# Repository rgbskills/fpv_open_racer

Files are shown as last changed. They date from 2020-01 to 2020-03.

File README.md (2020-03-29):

# Introduction
- Open source design for racing quad. You can download and modify the designs to your liking.
- **DXF** files are also available in `dxf/` - these are the files you send if you want to get them cut out of carbon (list of services are coming soon).
- **[Join our slack channel](https://join.slack.com/t/openfpvworkspace/shared_invite/enQtODgyMDY0MTgyNDAxLTNkYTExNzY0YzkxYjYwZTdiMzQ1MzkwNzc3OTJhODZiMTdiMTg1ZTQwYjM1NjA1ODZkYjUzNWY0YTA1NTUwZmE)**
- **[3D Preview](https://a360.co/2Fc0HBd)**
- **[Facebook page](https://www.facebook.com/openfpvcommunity)**

# Features
* **stretched X** - X=140 Y=180mm **wheelbase: 228mm** (more control on the roll axis)
* **Lots of space**, the idea is to have no zip ties and nothing attached to the top plate for easy servicing
* **Compatible with 5.1"** Props
* **Weight: 80g**
* **Arms can be easily swapped** without unscrewing the stack
* Both **20x20** and **30.5x30.5** Stack mounting options are supported
* **All screws are accessible** even after complete build
* **Easy stack access** - large 6mm holes on the bottom plate allows you to insert/remove screws that hold your stack without any hassle
* **28.5x45mm** hole pattern on the top plate to add Gopro mounts or any other 3d Printed add-ons
* **CNC Millable with 3mm bit**

# Recommendations
* Use a three level stack: ESC, FC, and the last level should contain your VTX and RX
* If you use a buzzer get a small 9*5.5mm one
* UFL or MMCX VTX antenna
* there are no zip tie slots for a reason
* Nothing should be mounted on the top plate unless its a stand alone component like an HD camera.

# Carbon parts
* **BASE plate - 2mm**
* **BOTTOM plate - 2mm**
* **TOP plate - 2mm**
* **ARM - 4mm**

# Bill of materials
* 4x 25mm Aluminium, standoffs [Banggood](https://www.banggood.com/Suleve-M3AS5-10Pcs-M3-25mm-Knurled-Standoff-Aluminum-Alloy-Anodized-Spacer-p-1118407.html?ID=223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)
* 8x 13-14mm M3 screws (arms) [Banggood](https://www.banggood.com/Suleve-M3CH10-50Pcs-M3-Carbon-Steel-Hex-Socket-Button-Round-Head-Cap-Screws-Bolts-4-20mm-Optional-Length-p-1232490.html?ID=513288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)
* 8x 6mm M3 screws (standoffs) [Banggood](https://www.banggood.com/Suleve-M3CH10-50Pcs-M3-Carbon-Steel-Hex-Socket-Button-Round-Head-Cap-Screws-Bolts-4-20mm-Optional-Length-p-1232490.html?ID=528721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)
* 8x M3 nylon insert nuts (arms) [Banggood](https://www.banggood.com/Suleve-CS1-50pcs-Carbon-Steel-Self-Locking-Hex-Nut-Nylon-Insert-Lock-Nut-M2M2_5M3M4M5M6M8M10M12-p-1499543.html?ID=514519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)
* 1x Buzzer [Banggood](https://www.banggood.com/5-PCS-Super-Loud-5V-Active-Alarm-Buzzer-Beeper-Tracker-95_5mm-for-Racing-Drone-p-1117207.html)
* 1x XT60 [Banggood](https://www.banggood.com/Amass-XT60-MaleFemale-Bullet-Connector-Plugs-For-RC-Lipo-Battery-p-929670.html)

# 3D printable parts
### (You can find all 3d printables under `accessories/3D/`)
* [Camera mount (micro)](https://www.thingiverse.com/thing:4080423)
- [XT60 mount](https://www.thingiverse.com/thing:4082915)

# Builds
Open Source - FPV racing frame

# Latest Render
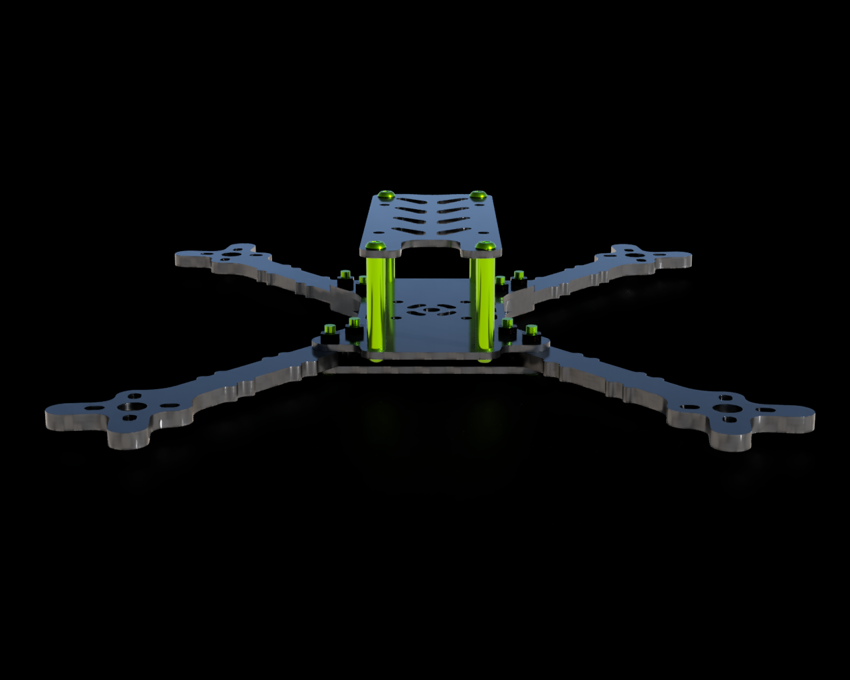
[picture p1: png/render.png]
Open Source - FPV racing frame


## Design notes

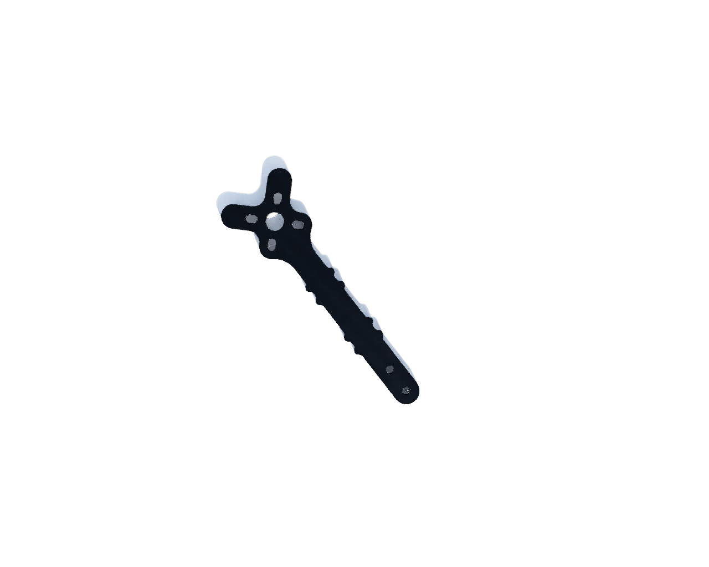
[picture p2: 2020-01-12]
png/ARM_4mm_4x.png

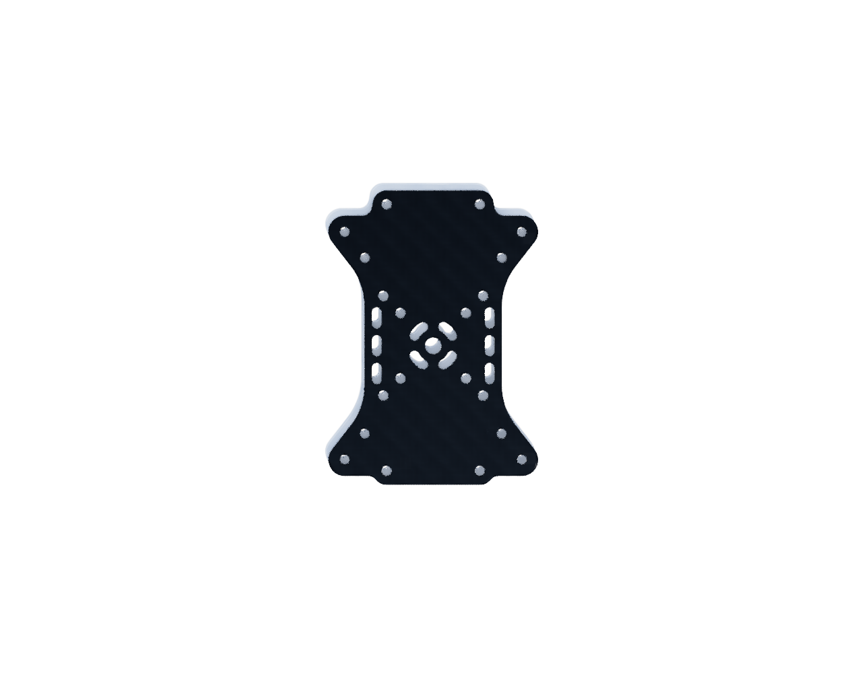
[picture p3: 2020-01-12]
png/BASE_2mm_1x.png

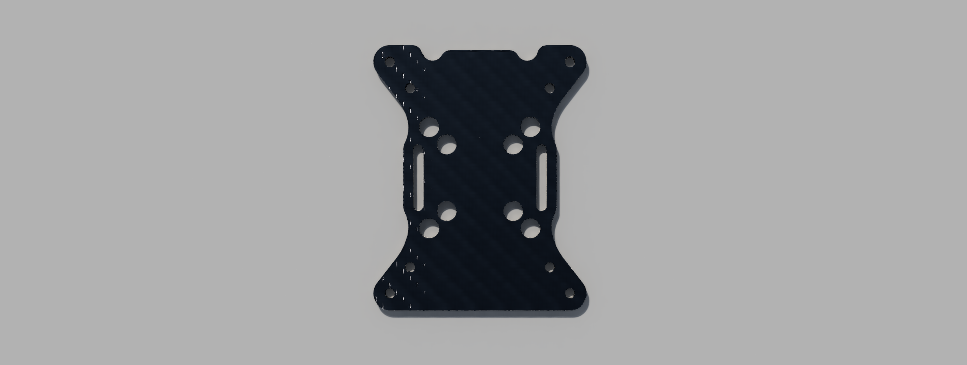
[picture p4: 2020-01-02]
png/BOTTOM_2mm_1x.png

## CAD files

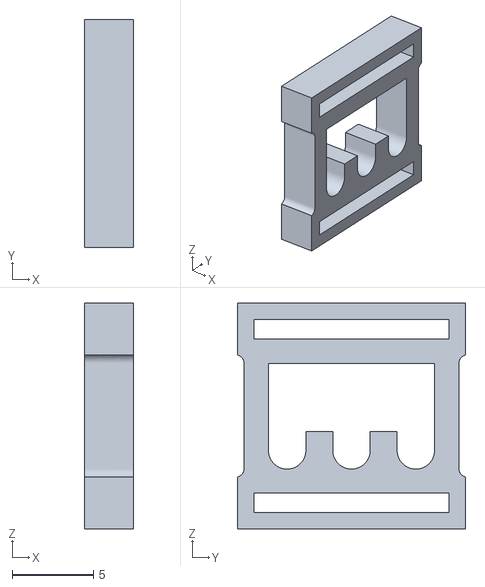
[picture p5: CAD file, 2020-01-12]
accessories/3D/cable_management_motor_ledTopBottom.stl
3.00 x 14.0 x 13.9

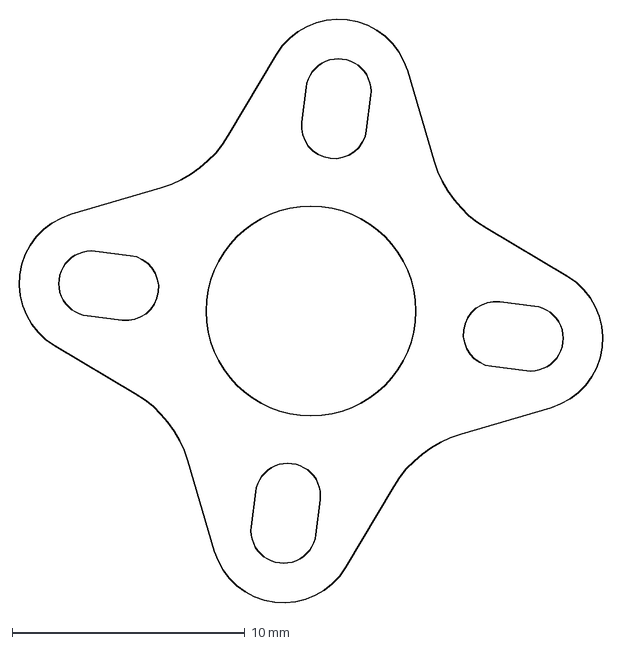
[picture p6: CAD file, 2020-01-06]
accessories/foamPads/motor_soft_mont.dxf
25.3 x 25.3 mm

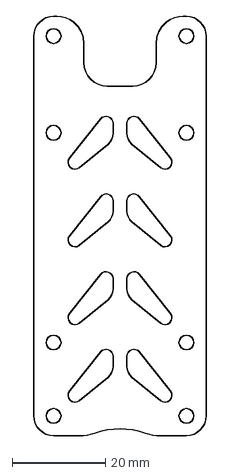
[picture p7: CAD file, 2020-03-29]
dxf/TOP_2mm_1x.dxf
37.0 x 90.0 mm

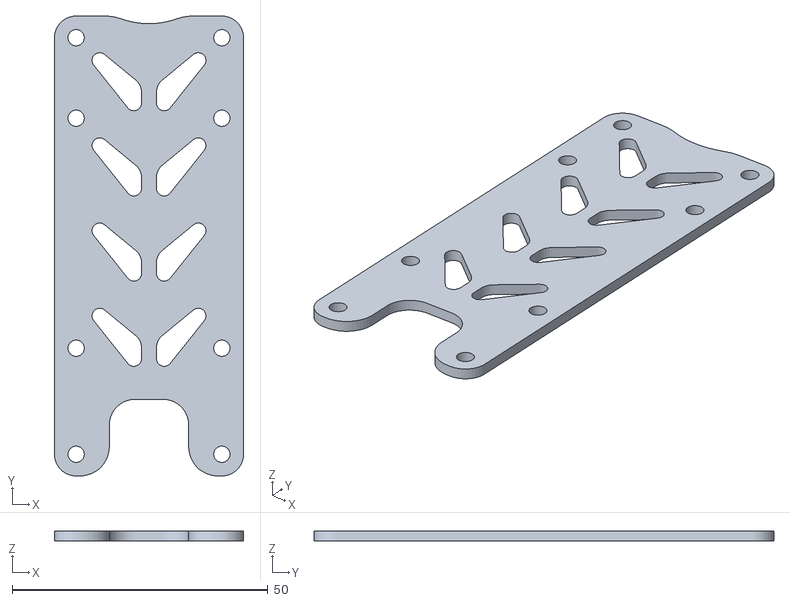
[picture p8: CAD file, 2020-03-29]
stl/top.stl
37.0 x 90.0 x 2.00

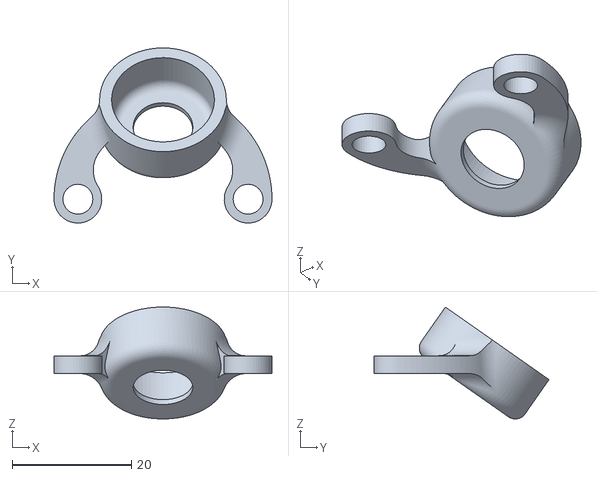
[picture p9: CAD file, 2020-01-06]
accessories/3D/mount_lolipop_UFL_MMCX.stl
36.5 x 29.3 x 18.7

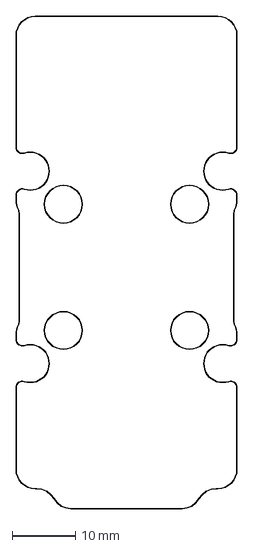
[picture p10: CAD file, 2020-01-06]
accessories/foamPads/bottom_plate_battery.dxf
35.0 x 78.0 mm

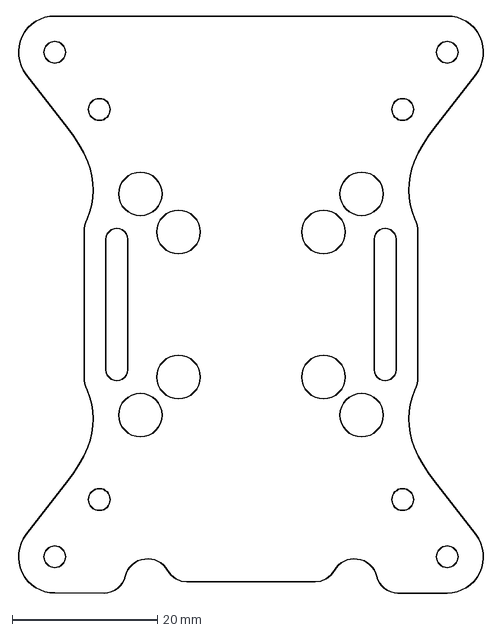
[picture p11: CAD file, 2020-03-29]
dxf/BOTTOM_2mm_1x.dxf
64.8 x 79.6 mm

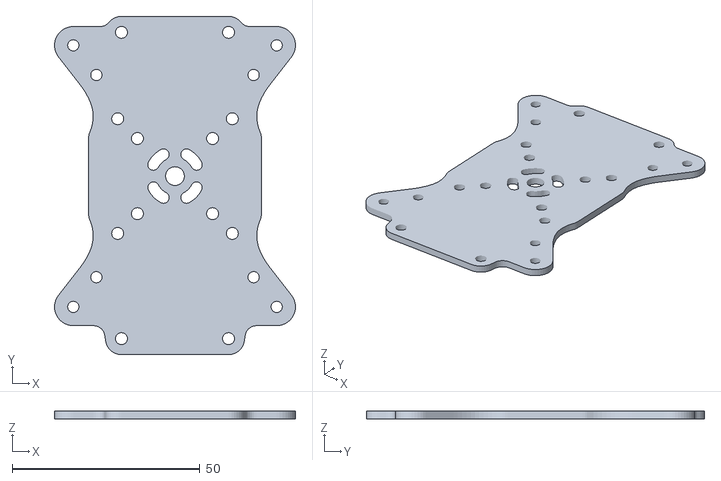
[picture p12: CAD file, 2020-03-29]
stl/base.stl
64.1 x 90.0 x 2.00

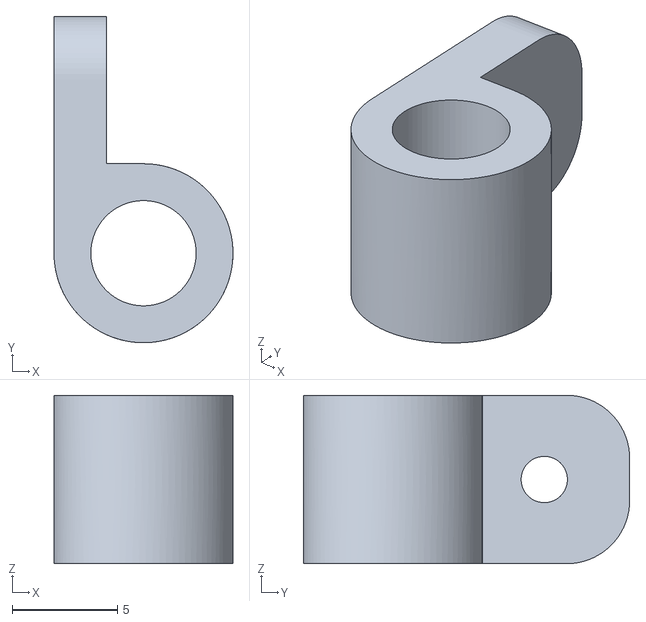
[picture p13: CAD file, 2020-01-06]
accessories/3D/mount_fpv_camera.stl
8.50 x 15.5 x 8.00

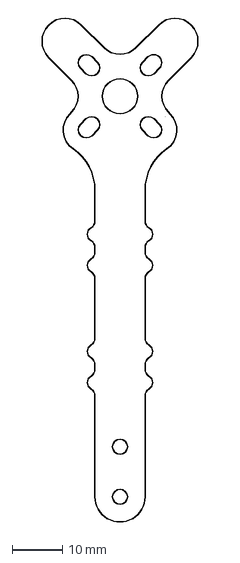
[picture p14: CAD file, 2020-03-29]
dxf/ARM_4mm_4x.dxf
32.0 x 101.2 mm

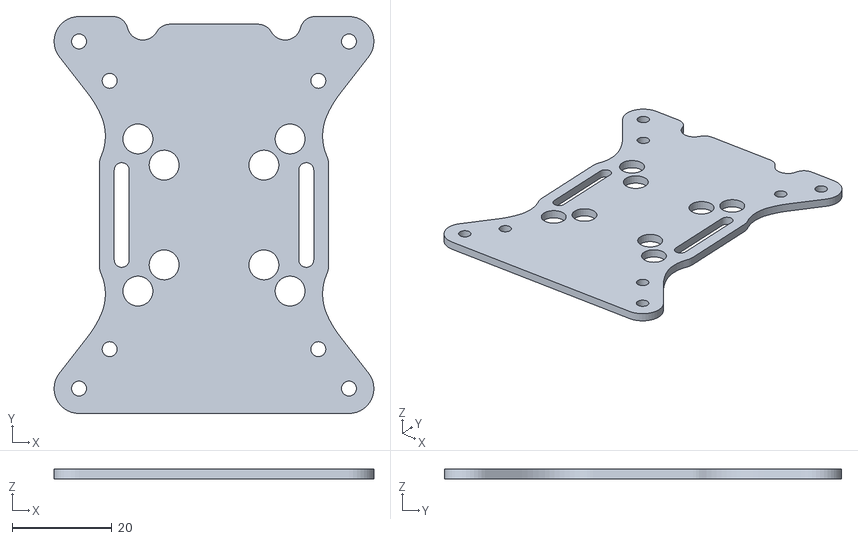
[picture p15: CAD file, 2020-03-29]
stl/bottom.stl
64.1 x 79.6 x 2.00

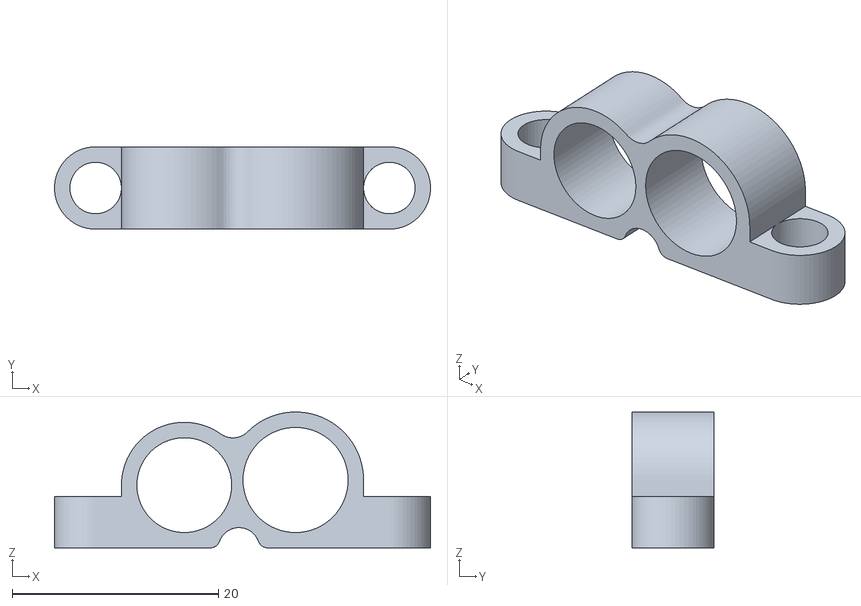
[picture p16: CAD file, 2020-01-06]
accessories/3D/mount_buzzer_capacitor.stl
36.5 x 8.00 x 13.2

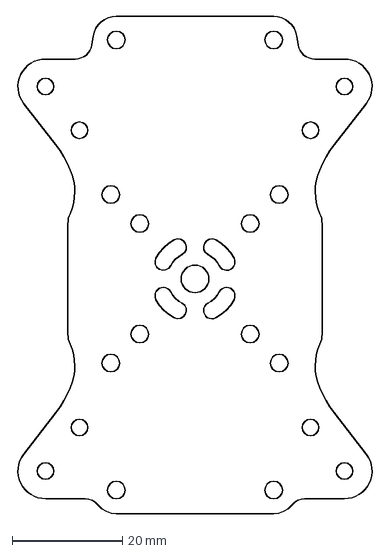
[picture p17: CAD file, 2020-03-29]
dxf/BASE_2mm_1x.dxf
64.8 x 90.0 mm

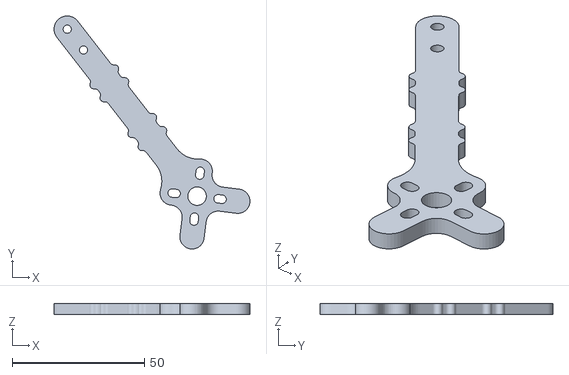
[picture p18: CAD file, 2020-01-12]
stl/arm.stl
74.1 x 88.1 x 4.00

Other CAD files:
accessories/3D/mount_xt60.stl
Open Racer.f3z

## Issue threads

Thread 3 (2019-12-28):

Bill of materials

stylesuxx, 2019-12-28:
I would re-name the requirements section to "Bill of materials" or BOM and maybe even link to a source to acquire the specific parts (at least those that are not so common, eg. the standoffs).

And by nylon nuts you mean nyloc nuts, no?

I think you also do not mention thickness of top and bottom plate - I assume they should be 2mm?

rgbskills, 2020-01-02:
Re-naming requirements to "Bill of materials" is a good idea. also, I'm all in on the linking stuff.

here is an example of the nuts I mentioned: https://armattanproductions.com/pages/hardware_details/10/47

I will work on some sort of image that shows assembly and material thickness and I also think we should mention it in the features section.

rgbskills, 2020-01-02:
Added links, renamed requirements section :)

Closed 2020-01-02.

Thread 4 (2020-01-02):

Battery strap insert slots.

rgbskills, 2020-01-02:
Battery strap slots are really good and they also make sure that the battery strap does not slip.
The battery strap should not touch the stack in any way, this way we can avoid the damaging of SMD components, also the strap can get wet that can also damage the stack.

Closed 2020-01-02.

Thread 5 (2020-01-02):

3 hole motor mount

rgbskills, 2020-01-02:
lose some weight.

stylesuxx, 2020-01-02:
I really like 4 mounting holes - 3 or even 2 mounting holes always make me super nervous. Maybe this could be optional?

rgbskills, 2020-01-02:
I'm getting mixed signals from the community I don't care for 3hole mount my self, we can make plenty of arm designs available, we need to decide on the official one.

so the question is:
should we go with a 3 hole mount or a 4 hole mount by default?

stylesuxx, 2020-01-02:
How much weight do we save by having 3 instead of 4 holes?

rgbskills, 2020-01-03:
I have no clue on how to calculate this, but something like 4g (I'm guessing)

stylesuxx, 2020-01-03:
My ghetto approach would be to load both stl's in the slicer, set 100%
infill, density of CF and see what it spits out.

The less hacky solution would be to do it in fusion - they do have lot's of
physics tests in there - no?

Hali <notifications@github.com> schrieb am Fr., 3. Jän. 2020, 12:01:

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

rgbskills, 2020-01-05:
The difference is 8-10g. I did the math :))

rgbskills, 2020-01-05:
It's not worth the risk, a two-hole version would mather from a weight perspective, but that would compromise the structural integrity of the frame.I'm changing the official version back to a full four-hole system.

I'm planning to create a wizard that will optimize the frame to the specific requirements of the user Like if you want zip tie holes or printed parts, camera mounting solution, number of holes for motors and more...

stylesuxx, 2020-01-05:
@rgbskills Wizzard sounds really cool.

What is the total weight of the frame, including hardware? I mean if the aim is a racing frame and the arms are easy to swap anyways, maybe 8-10g are worth it ;-) Bob Roogies new 3" frame for example only has two motor holes at all and still seems to be sturdy.

rgbskills, 2020-01-06:
The motor is more protected with all screws inserted, you are losing the carbon anyway. It's better to have it there. I yet to receive the carbon version, I can only give an answer once I receive the frame. Until then it's just speculation but it should be around 250-300g

stylesuxx, 2020-01-06:
I'll order some 4mm carbon, then I can rapidly prototype the arms...

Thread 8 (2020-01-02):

Battery top mount

stylesuxx, 2020-01-02:
Just putting it out there - I like my batteries on the top. Maybe once the racer is *"done"* you could adapt it to a freestyler. I would assume, that the arms for example could be re-used

rgbskills, 2020-01-06:
fpv_open_freestyler sounds like a new project, maybe interchangeable parts like arms and 3d printables.

Closed 2020-01-07.

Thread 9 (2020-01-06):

Arm protectors

stylesuxx, 2020-01-06:
I think it would be cool to have some TPU arm protectors, they could also have a second purpose for soft-mounting the motors. Something like that => https://www.thingiverse.com/thing:2770012

rgbskills, 2020-01-07:
I added a soft mounting design that you can cut with any laser, even a blue diode laser should handle a 2mm foam. you can find it here: https://github.com/rgbskills/fpv_open_racer/tree/master/accessories/foamPads

If you don't have a laser then you can cut it with an Exacto knife.

I will soon design a 3D printable version and until then this ticket remains open :))

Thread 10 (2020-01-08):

Stack

stylesuxx, 2020-01-08:
I think it would be a good thing to mention that a 3 high stack (30x30 or 20x20) is recommended:
1. ESC
2. FC
3. VTX

Otherwise it might be really tight to fit the VTX.

rgbskills, 2020-01-08:
I agree.

Closed 2020-01-10.

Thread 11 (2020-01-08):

Customizable Buzzer/Cap mount

stylesuxx, 2020-01-08:
I think it would be cool to have a customizable Buzzer/Cap mount, just in case if someone has problem with the hole sizes. I can whip something up in openSCAD that is similar to your design and put it up on thingiverse where one can use the customizer.

Maybe it would also be a good idea to link matching (that will fit the default holes) buzzer and cap in the BOM.

rgbskills, 2020-01-08:
Sounds good, I measured most of the caps I had in the house and they all seem to be the same diameter +/- 0.2 so it should be fine, the buzzers I have are smaller, https://www.banggood.com/5V-Buzzer-Alarm-Beeper-With-Cable-for-Eachine-QX70-QX90-QX95-NAZE32-F3-DIY-Micro-Brushed-FPV-Racer-p-1100338.html

This is cheap (I bought it for 0.99 it's now 2.15 for some reason) , and a full-size buzzer is gigantic compared to this. and most racers use this one. I tried fitting a full-sized one and there is just not enough space.

a better offer can always be found on banggood: https://www.banggood.com/5-PCS-Super-Loud-5V-Active-Alarm-Buzzer-Beeper-Tracker-95_5mm-for-Racing-Drone-p-1117207.html

stylesuxx, 2020-01-09:
OK, sounds great. Then I would add the links to the buzzer to the BOM.

Closed 2020-01-09.

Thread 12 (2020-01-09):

XT60 printable

stylesuxx, 2020-01-09:
I am using Amass XT60 connectors that come [with an extra cover](https://www.3dxr.co.uk/wp-content/uploads/2017/04/Amass-XT60.jpg), so the front part is a little bit shorter. I would need the XT60 printable 3.3mm shorter than the current one.

The geometry is also slightly different, but the plug still fits.

I would link the recommended XT60 connector in the BOM.

Closed 2020-01-09.

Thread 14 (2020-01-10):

Wire management on the arms

stylesuxx, 2020-01-10:
Regarding the new wire management on the arms:
* Would it not be enough for the notches to only be on one side? Since the arm is symmetrical you can flip it in the direction you want the notches to be on
* Chamfered edges: I am not sure if it is a good idea to have two 90 degree turns over unchamfered edges, I am afraid that the edges would potentially cut into the wire
* The second set of notches, close to the base plate - is this even necessary? From what I understand the motor wires goes in between the two plates and come out just beneath the stack - would it then not be easier to just have one notch at the end of the arm since you then follow the arm beneath the plates anyways

rgbskills, 2020-01-11:
This came to me in a dream :)) did it in a morning a few hours before I went to work. I will print all the options and test which one is better, I will follow uo with some pictures.

rgbskills, 2020-01-12:
After a lot of experimentation, I tried one sided, double sided, none, and more I found double sided to work the best I even moved it up a little, it's not centered, it's just the right distance from the motor and the base so that if a prop bends it wont hit the slots. I also tried to cut the motor cable on carbon and the only way I succeeded if i pressed super hard on it and moved it around.
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

stylesuxx, 2020-01-12:
I see - I think I just misunderstood how the cable management should work. i was under the impression, that the wire is put into the groove. I always use electrical tape to mount my wires and don't use LED's. Makes sense to me now.

rgbskills, 2020-01-13:
LED's are more popular in racing so I definitely wanted to support a solid way to mount things on the arms. It looks a bit out of the ordinary because I also would like to support 3mm bit milling. It's as low profile as it gets and I hope I got the spacing right :))

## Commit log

2019-12-25 Add fusion360 file
    [Open Racer.f3z]
2019-12-25 Add render of frame
2019-12-25 Add DXF files
    [ARM_4mm_4x.dxf, BASE_2mm_1x.dxf, BOTTOM_2mm_1x.dxf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]
2019-12-26 Add more space between screws on the arms, modify pattern on top plate, More solid base plate
    [ARM_4mm_4x.dxf, BASE_2mm_1x.dxf, BOTTOM_2mm_1x.dxf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]
2019-12-27 Lenghten arm bolt spacing 10mm, update render and dxf, add stl files
    [ARM_4mm_4x.dxf, BASE_2mm_1x.dxf, BOTTOM_2mm_1x.dxf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]
2020-01-02 Add battery strap slot to bottom plate, modify arms to 3 hole motor mount, support 3mm bit CNC milling
    [ARM_4mm_4x.dxf, BASE_2mm_1x.dxf, BOTTOM_2mm_1x.dxf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]
2020-01-02 Update README.md
    @stylesuxx re-named requirements to "Bill of materials" as you recommended, also added a section that makes the carbon parts thickness clear.
2020-01-04 Remove Vbat cable cutout from base plate
    [BASE_2mm_1x.dxf, base.stl]
2020-01-04 Update fusion archive
    [Open Racer.f3z]
2020-01-06 Add accessories, center addon mounting on top plate, make top plate back cutout smaller, add 4 hole motor mount
    [Open Racer.f3z, TOP_2mm_1x.dxf, arm.stl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]
2020-01-06 Fix stl bottom and base naming
    [base.stl, bottom.stl]
2020-01-08 Remove accesories from main file, remove broken gopro mount
    [Open Racer.f3z, mount_gopro_session.stl]
2020-01-09 Fixed screw links
2020-01-10 Add motor cable management
    [ARM_4mm_4x.dxf, BASE_2mm_1x.dxf, arm.stl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]
2020-01-10 Update fusion archive for motor cable management
    [Open Racer.f3z]
2020-01-12 Add LED wire cable management
    [BASE_2mm_1x.dxf, Open Racer.f3z, base.stl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]
2020-01-12 Adjust arm cable management distance from base, add aditional cable management holes on base
    [ARM_4mm_4x.dxf, BASE_2mm_1x.dxf, Open Racer.f3z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]
2020-03-29 Fix bottom battery slot, fix arm screw holes, Remove cable guides from main plate, update readme
    [ARM_4mm_4x.dxf, ARM_4mm_4x_.dxf, BASE_2mm_1x.dxf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]
